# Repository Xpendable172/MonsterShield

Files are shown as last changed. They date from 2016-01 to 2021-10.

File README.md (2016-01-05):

# MonsterShield

    MonsterShield Prop Controller Editor software
    Copyright (C) 2015  Jason LeSueur Tatum

    This program is free software: you can redistribute it and/or modify
    it under the terms of the GNU General Public License as published by
    the Free Software Foundation, either version 3 of the License, or
    (at your option) any later version.

    This program is distributed in the hope that it will be useful,
    but WITHOUT ANY WARRANTY; without even the implied warranty of
    MERCHANTABILITY or FITNESS FOR A PARTICULAR PURPOSE.  See the
    GNU General Public License for more details.

    You should have received a copy of the GNU General Public License
    along with this program.  If not, see <http://www.gnu.org/licenses/>.

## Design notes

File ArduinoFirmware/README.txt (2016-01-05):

/**    
	MonsterShield Prop Controller Editor software
    Copyright (C) 2015  Jason LeSueur Tatum

    This program is free software: you can redistribute it and/or modify
    it under the terms of the GNU General Public License as published by
    the Free Software Foundation, either version 3 of the License, or
    (at your option) any later version.

    This program is distributed in the hope that it will be useful,
    but WITHOUT ANY WARRANTY; without even the implied warranty of
    MERCHANTABILITY or FITNESS FOR A PARTICULAR PURPOSE.  See the
    GNU General Public License for more details.

    You should have received a copy of the GNU General Public License
    along with this program.  If not, see <http://www.gnu.org/licenses/>.
**/

  MonsterShield Firmware Library V 1.5.0 {BETA}
  //////////////////////////////////////////////////////////////// 
  Released:   September 4, 2013
  Author:     Jason LeSueur Tatum
  
  HauntSoft 
  http://www.hauntsoft.com
  P.O. Box 1475
  Arlington Heights, IL 60006
  
  This library is intended to be used with the MonsterShield line of
  products produced by HauntSoft and is provided AS-IS.  This
  code has only been tested with Arduino UNO REV 3 microcontrollers,
  but may work with other Arduino compatible boards.
  
  The MonsterShield firmware is built around the "MonsterShield"
  class that provides access to all functionality and hardware.
  
  You are free to use this firmware in any way you see fit.  It 
  is as easy as instantiating a MonsterShield class object and 
  calling the "init()" function in your setup() routine.
  
  Tutorials and example solutions using this library
  will be made available over time on http://www.hauntsoft.com

  Arduino UNO R3 Pin Usage
  ===================================
  Digital I/O Pins
  ===================================
  13 LED2
  12 Keypad 0 (Prev      / Out 1)
  11 Keypad 1 (Next      / Out 2)
  10 Keypad 2 (Enable    / Out 3)
  9  Keypad 3 (Play/Stop / Out 4)
  8  Keypad 4 (Record)
  7  <---- Unused
  6  <---- Unused
  5  <---- Unused
  4  <---- Unused
  3  TX (Serial to MP3 module)
  2  RX (Serial from MP3 module, not connected)
  1  TX (Serial to host computer)
  0  RX (Serial to host computer)
  
  ===================================
  Analog I/O Pins
  ===================================
  A0 Trigger 0 (MonsterShield)
  A1 Trigger 1 (MonsterShield Expander)
  A2 Trigger 2 (MonsterShield Expander)
  A3 Trigger 3 (MonsterShield Expander)
  A4  SCL (i2c bus)
  A5  SDA (i2c bus)

  How to use the MonsterShield with the 1.5.0 firmware:
  =====================================================
  There are a few differences in how the MonsterShield 
  works with this new firmware compared to previous versions of the firmware.
  This is a quick guide to the new changes:
  
  Factory Reset:
  --------------
  1. Hold down the middle (prev/enable) button while pressing reset
  2. Release middle (prev/enable) button when "F" flashes rapidly
  3. When "F" flashes once per second, select number of desired slots
     by scrolling up and down with prev and nxt buttons.  Confirm
     desired number of slots by pressing mode/trigger button.
     Available options are: 1,2,3,4,5,6,7,8,9,A,B,C,D,E,F
     Note: If no selection is made for 10 seconds, then the value displayed
     will automatically be selected.
  4. Factory Reset will complete and the display will show "0" when done.
  
  Maximum slot length:
  ---------------------
  The maximum length of animation per slot depends on 2 factors:   
  1.  The number of slots the MonsterShield is configured for.
      You can perform a factory reset to change this number.  You can
      select 1 through 15 slots.
  2.  If you have the MonsterShield Expander board, you can increase
      the available slot length depending on whether you have 
      1, 2, or 3 total EEPROM chips installed.
  3.  A future version of the firmware will allow for larger EEPROM chips,
      but right now it is assumed that only the 24LC256 (32kbyte) chip
      is supported.
      
      Note:  The reason there is no difference between some slot
      numbers and/or chips is because we do not allow an animation
      to be split across multiple EEPROM chips.  We also enforce
      that all slots are equally sized.  There is also a requirement
      that each slot be divided evenly in 64-byte page increments.
      
This chart shows you your maximum available slot lengths:
slots	1 chip   2 chips  3 chips
15    00:54.4	 0:01:41  0:02:43
14    00:57.6	 0:01:55  0:02:43
13    01:02.4	 0:01:55  0:02:43
12    01:07.2	 0:02:16  0:03:23
11    01:13.6	 0:02:16  0:03:23
10    01:21.6	 0:02:43  0:03:23
9     01:29.6	 0:02:43  0:04:32
8     01:40.8	 0:03:23  0:04:32
7     01:55.2	 0:03:23  0:04:32
6     02:16.0	 0:04:32  0:06:48
5     02:43.2	 0:04:32  0:06:48
4     03:23.2	 0:06:48  0:06:48
3     04:32.0	 0:06:48  0:13:36
2     06:48.0	 0:13:36  0:13:36
1     13:36.0	 0:13:36  0:13:36
 
  Recording animation with the keypad:
  --------------------
  With previous versions of the firmware, all you had to do is press the 
  "record" button on the keypad and begin pressing the output buttons
  to record the animation.  With the new firmware, things are a bit
  more complex because there we've greatly increased the capabilities:
  
  * The new firmware supports the addition of up to 3 extra relay banks 
    (each bank contains 4 output relays) for a total of 16 relays when
    the MonsterShield Expander board is employed.
    
  * You can now record a single relay output at a time without affecting
    animation already recorded on the other tracks.  
    
  * You can now lay down additional recording on a track (overlay) 
    without losing the animation already stored on that track.  This can be
    used to extend an animation longer (up to the maximum length as given
    in the chart above)
    
  Recording steps:
  1.  Press the "record" button on the keypad.
  2.  "b" begins flashing.  This is bank-select mode.  Press 
      out 1, out 2, out 3, or out 4 to select banks 0, 1, 2, or 3.  Press
      "record" again to confirm.
  3.  "r" begins flashing.  This is relay-select mode.  Press
      out 1, out 2, out 3, or out 4 to select which relay on the selected
      bank you want to record.  If you'd like to record all 4 relays
      at the same time (like the old firmware), then skip this selection
      and just press "record" again.
  4.  "c" begins flashing.  This is the clear-option.  
      i.  Press out 1 to select overlay mode (record on top of track data)
      ii. Press out 2 to select clear track mode (erase selected track)
      iii.Press out 3 to select clear entire animation slot.

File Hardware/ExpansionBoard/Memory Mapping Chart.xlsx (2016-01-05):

memory | Control page size | avail mem | bytes per event | slots | Bytes per event | Pages | Actual bytes per slot | Actual events | Actual used memory | Wasted bytes | events/sec | Secs/Slot | Time/Slot | 2X Events | Bank 0 | Bank 1 |  |  |  |  | Bank 0 | Bank 1 | Bank 2
32768 | 128 | 32640 | 2 | 15 | 2176 | 34 | 2176 | 1088 | 32640 | 0 | 20 | 54.4 | 0:00:54 | 2176 | 7 | 8 | 4080 | 63 | 2016 | 0:01:41 | 5 | 5 | 5 | 6528 | 102 | 3264 | 0:02:43
32768 | 128 | 32640 | 2 | 14 | 2331 | 36 | 2304 | 1152 | 32256 | -384 | 20 | 57.6 | 0:00:58 | 2304 | 7 | 7 | 4662 | 72 | 2304 | 0:01:55 | 4 | 5 | 5 | 6528 | 102 | 3264 | 0:02:43
32768 | 128 | 32640 | 2 | 13 | 2510 | 39 | 2496 | 1248 | 32448 | -192 | 20 | 62.4 | 0:01:02 | 2496 | 6 | 7 | 4662 | 72 | 2304 | 0:01:55 | 4 | 4 | 5 | 6528 | 102 | 3264 | 0:02:43
32768 | 128 | 32640 | 2 | 12 | 2720 | 42 | 2688 | 1344 | 32256 | -384 | 20 | 67.2 | 0:01:07 | 2688 | 6 | 6 | 5440 | 85 | 2720 | 0:02:16 | 4 | 4 | 4 | 8160 | 127 | 4064 | 0:03:23
32768 | 128 | 32640 | 2 | 11 | 2967 | 46 | 2944 | 1472 | 32384 | -256 | 20 | 73.6 | 0:01:14 | 2944 | 5 | 6 | 5440 | 85 | 2720 | 0:02:16 | 3 | 4 | 4 | 8160 | 127 | 4064 | 0:03:23
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

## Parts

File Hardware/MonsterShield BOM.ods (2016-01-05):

 |  |  |  | # of Units: | 100 |  |  |  | 200 |  |  |  | 200 |  |  |  | 10
 |  |  |  |  |  |  |  |  | Imagineering |  |  |  | PCB Universe
MonsterShield PCB
MFG part# | Digikey part# | Reference # | Type | Unit quantity | Extend Qty | Unit Price | Extend Price | Cost per Unit | Extend Qty | Unit Price | Extend Price | Cost per Unit | Extend Qty | Unit Price | Extend Price | Cost per Unit | Extend Qty | Unit Price | Extend Price | Cost per Unit
 |  |  | PCB (MonsterShield) | 1 | 100 | 4.5 | 450 | 4.5 | 200 | 2.5 | 500 | 2.5 | 200 | 2.02 | 404 | 2.02 | 10 | 2.02 | 20.2 | 2.02
 |  |  |  |  |  |  | 450 | 4.5 |  |  | 500 | 2.5 |  |  | 404 | 2.02 |  |  | 20.2 | 2.02
MonsterShield Main Parts
MFG part# | Digikey part# | Reference # | Type | Unit quantity | Extend Qty | Unit Price | Extend Price | Cost per Unit | Extend Qty | Unit Price | Extend Price | Cost per Unit | Extend Qty | Unit Price | Extend Price | Cost per Unit | Extend Qty | Unit Price | Extend Price | Cost per Unit
A31412-ND | A31412-ND | RJ45 Keypad | RJ45 connector vertical | 1 | 100 | 0.7628 | 76.28 | 0.7628 | 200 | 0.69348 | 138.696 | 0.69348 | 200 | 0.62412 | 124.824 | 0.62412 | 10 | 0.884 | 8.84 | 0.01768
LA-401VN | 511-1531-ND (http://www.digikey.com/scripts/DKSearch/dksus.dll?Detail&itemSeq=116038993&uq=634756494036963984) | 7 Segment 10 DIP 7.62mm | 7 segment display, red | 1 | 100 | 1.575 | 157.5 | 1.575 | 200 | 1.4 | 280 | 1.4 | 200 | 1.225 | 245 | 1.225 | 10 | 1.96 | 19.6 | 0.0392
 | A100204-ND | 24LC256 | CONN IC socket vert 8POS Tin | 1 | 100 | 0.1255 | 12.55 | 0.1255 | 200 | 0.111 | 22.2 | 0.111 | 200 | 0.10618 | 21.236 | 0.10618 | 10 | 0.181 | 1.81 | 0.00362
 | 490-1532-1-ND | C1,C2,C3 | Ceramic Capacitor .1uF 0603 SMT | 3 | 300 | 0.0088 | 2.64 | 0.0264 | 600 | 0.00616 | 3.696 | 0.01848 | 600 | 0.0048 | 2.88 | 0.0144 | 30 | 0.00368 | 0.1104 | 0.0002208
 | A98037-ND | J1 Trigger | Screw terminal - 3 pins | 1 | 100 | 0.5595 | 55.95 | 0.5595 | 200 | 0.5108 | 102.16 | 0.5108 | 200 | 0.48648 | 97.296 | 0.48648 | 10 | 0.73 | 7.3 | 0.0146
 | 609-3263-ND | J2 Relays | Generic male header - 6 pins | 1 | 100 | 0.1563 | 15.63 | 0.1563 | 200 | 0.13824 | 27.648 | 0.13824 | 200 | 0.13222 | 26.444 | 0.13222 | 10 | 0.13222 | 1.3222 | 0.0026444
 | S5456-ND | J3 MP3 Module | Generic female header right angle- 20 pins | 1 | 100 | 0.9144 | 91.44 | 0.9144 | 200 | 0.84328 | 168.656 | 0.84328 | 200 | 0.762 | 152.4 | 0.762 | 10 | 1.219 | 12.19 | 0.02438
 | CP1-3524NG-ND | J4 Audio | Stereo Jack (TRS) 3.5mm | 1 | 100 | 0.3995 | 39.95 | 0.3995 | 200 | 0.323 | 64.6 | 0.323 | 200 | 0.323 | 64.6 | 0.323 | 10 | 0.595 | 5.95 | 0.0119
 | 475-1410-1-ND | LED1,LED2 | green smd LED | 2 | 200 | 0.059 | 11.8 | 0.118 | 400 | 0.05164 | 20.656 | 0.10328 | 400 | 0.0472 | 18.88 | 0.0944 | 20 | 0.074 | 1.48 | 0.00296
 | MCP23017-E/SS-ND | MCP23017 | SSOP28DB | 1 | 100 | 0.95 | 95 | 0.95 | 200 | 0.95 | 190 | 0.95 | 200 | 0.95 | 190 | 0.95 | 10 | 1.26 | 12.6 | 0.0252
 | P4.7KGCT-ND | R1, R2 | 4.7k Ω Resistor, 0603 SMT | 2 | 200 | 0.007 | 1.4 | 0.014 | 400 | 0.00384 | 1.536 | 0.00768 | 400 | 0.00256 | 1.024 | 0.00512 | 20 | 0.00152 | 0.0304 | 0.0000608
 | P1.0KGCT-ND | R3 | 1k Ω Resistor, 0603 SMT | 1 | 100 | 0.007 | 0.7 | 0.007 | 200 | 0.0052 | 1.04 | 0.0052 | 200 | 0.00384 | 0.768 | 0.00384 | 10 | 0.00152 | 0.0152 | 0.0000304
 | P220GCT-ND | R4, R5, R6, R7, R8, R9, R10, R11, R12, R13, R14, R15, R16, R17 | 150 Ω Resistor, 0603 SMT | 14 | 1400 | 0.00256 | 3.584 | 0.03584 | 2800 | 0.00256 | 7.168 | 0.03584 | 2800 | 0.00152 | 4.256 | 0.02128 | 140 | 0.00152 | 0.2128 | 0.0004256
 | SW402-ND | S1, S2, S3,RESET | Pushbutton | 4 | 400 | 0.23836 | 95.344 | 0.95344 | 800 | 0.18927 | 151.416 | 0.75708 | 800 | 0.18927 | 151.416 | 0.75708 | 40 | 0.2524 | 10.096 | 0.020192
 |  |  |  |  |  |  | 659.768 | 6.59768 |  |  | 1179.472 | 5.89736 |  |  | 1101.024 | 5.50512 |  |  | 81.557 | 8.1557
MonsterShield Additional parts
MFG part# | Digikey part# | Reference # | Type | Unit quantity | Extend Qty | Unit Price | Extend Price | Cost per Unit | Extend Qty | Unit Price | Extend Price | Cost per Unit | Extend Qty | Unit Price | Extend Price | Cost per Unit | Extend Qty | Unit Price | Extend Price | Cost per Unit
 | 24LC256-I/P-ND | 24LC256 | 24LC256 32k EEPROM chip | 1 | 100 | 0.81 | 81 | 0.81 | 200 | 0.81 | 162 | 0.81 | 200 | 0.81 | 162 | 0.81 | 10 | 0.88 | 8.8 | 0.88
 | SainSmart 4-Relay Module |  | SAINSMART | 1 | 100 | 8 | 800 | 8 | 200 | 8 | 1600 | 8 | 200 | 8 | 1600 | 8 | 10 | 8 | 80 | 8
 | 609-4453-1-ND | Female pins | Female pins for ribbon cable assembly | 12 | 1200 | 0.08494 | 101.928 | 1.01928 | 2400 | 0.08494 | 203.856 | 1.01928 | 2400 | 0.08494 | 203.856 | 1.01928 | 120 | 0 | 0 | 0
 | 609-2337-ND | 6-pin Connector housings | 6-pin Connector housings | 2 | 200 | 0.6232 | 124.64 | 1.2464 | 400 | 0.6232 | 249.28 | 1.2464 | 400 | 0.6232 | 249.28 | 1.2464 | 20 | 0 | 0 | 0
 | (futurelec GRCABLE10) | 6" ribbon cable | 6" ribbon cable (0.40 cents per 1 meter) | 1 | 100 | 0.07 | 7 | 0.07 | 200 | 0.07 | 14 | 0.07 | 200 | 0.07 | 14 | 0.07 | 10 | 0 | 0 | 0
 | 609-3249-ND | gold-plated headers, 6-pin | gold-plated headers, 6-pin | 2 | 200 | 0.2619 | 52.38 | 0.5238 | 400 | 0.2352 | 94.08 | 0.4704 | 400 | 0.2352 | 94.08 | 0.4704 | 20 | 0 | 0 | 0
 | 609-3300-ND | gold-plated headers, 8-pin | gold-plated headers, 8-pin | 2 | 200 | 0.2646 | 52.92 | 0.5292 | 400 | 0.2376 | 95.04 | 0.4752 | 400 | 0.2376 | 95.04 | 0.4752 | 20 | 0 | 0 | 0
 | 609-3465-ND | gold-plated breakaway 36-pin | gold-plated breakaway 36-pin | 1 | 100 | 0 | 0 | 0 | 200 | 0 | 0 | 0 | 200 | 0 | 0 | 0 | 10 | 0.707 | 7.07 | 0.707
 | Adafruit (206) | 6" cable with .100" 6 position | 6" cable with .100" 6 position | 1 | 100 | 0 | 0 | 0 | 200 | 0 | 0 | 0 | 200 | 0 | 0 | 0 | 10 | 1.5 | 15 | 1.5
 |  | Printed quickstart guide 1 page | Printed quickstart guide 1 page | 1 | 100 | 0.01 | 1 | 0.01 | 200 | 0.01 | 2 | 0.01 | 200 | 0.01 | 2 | 0.01 | 10 | 0 | 0 | 0
 |  |  |  |  |  |  | 1220.868 | 12.20868 |  |  | 2420.256 | 12.10128 |  |  | 2420.256 | 12.10128 |  |  | 110.87 | 11.087
Keypad PCB
MFG part# | Digikey part# | Reference # | Type | Unit quantity | Extend Qty | Unit Price | Extend Price | Cost per Unit | Extend Qty | Unit Price | Extend Price | Cost per Unit | Extend Qty | Unit Price | Extend Price | Cost per Unit | Extend Qty | Unit Price | Extend Price | Cost per Unit
 |  |  | PCB (Keypad) | 1 | 100 | 4.5 | 450 | 4.5 | 200 | 2.5 | 500 | 2.5 | 200 | 1.27 | 254 | 1.27 | 10 | 1.27 | 12.7 | 1.27
 |  |  |  |  |  |  | 450 | 4.5 |  |  | 500 | 2.5 |  |  | 254 | 1.27 |  |  | 12.7 | 1.27
Keypad Parts
MFG part# | Digikey part# | Reference # | Type | Unit quantity | Extend Qty | Unit Price | Extend Price | Cost per Unit | Extend Qty | Unit Price | Extend Price | Cost per Unit | Extend Qty | Unit Price | Extend Price | Cost per Unit | Extend Qty | Unit Price | Extend Price | Cost per Unit
 | A31442-ND | RJ45 Keypad | RJ45 connector right-angle | 1 | 100 | 1.0408 | 104.08 | 1.0408 | 200 | 0.94616 | 189.232 | 0.94616 | 200 | 0.85154 | 170.308 | 0.85154 | 10 | 1.206 | 12.06 | 1.206
 | SW402-ND | OUT1,OUT2,OUT3,OUT4,REC | Pushbutton | 5 | 500 | 0.2103 | 105.15 | 1.0515 | 1000 | 0.18927 | 189.27 | 0.94635 | 1000 | 0.18927 | 189.27 | 0.94635 | 50 | 0.2524 | 12.62 | 1.262
 |  |  |  |  |  |  | 209.23 | 2.0923 |  |  | 378.502 | 1.89251 |  |  | 359.578 | 1.79789 |  |  | 24.68 | 2.468
Packaging
MFG part# | Digikey part# | Reference # | Type | Unit quantity | Extend Qty | Unit Price | Extend Price | Cost per Unit | Extend Qty | Unit Price | Extend Price | Cost per Unit | Extend Qty | Unit Price | Extend Price | Cost per Unit | Extend Qty | Unit Price | Extend Price | Cost per Unit
 | SCP313-ND |  | Anti-static bag, 4" x 6" | 1 | 100 | 0.0612 | 6.12 | 0.0612 | 200 | 0.0612 | 12.24 | 0.0612 | 200 | 0.0612 | 12.24 | 0.0612 | 10 | 0.0612 | 0.612 | 0.0612
 |  |  | corrugated mailable white box (size?) | 1 | 100 | 1 | 100 | 1 | 200 | 1 | 200 | 1 | 200 | 1 | 200 | 1 | 10 | 1.5 | 15 | 1.5
 |  |  |  |  |  |  | 106.12 | 1.0612 |  |  | 212.24 | 1.0612 |  |  | 212.24 | 1.0612 |  |  | 15.612 | 1.5612
Optional Parts
Item # | Description |  | Source | Unit quantity | Extend Qty | Unit Price | Extend Price | Cost per Unit | Extend Qty | Unit Price | Extend Price | Cost per Unit | Extend Qty | Unit Price | Extend Price | Cost per Unit | Extend Qty | Unit Price | Extend Price | Cost per Unit
 | Arduino |  | AMAZON | 1 | 100 | 20 | 2000 | 20 | 200 | 20 | 4000 | 20 | 200 | 20 | 4000 | 20 |  |  |  |  | ARDUR3
A98374-ND | Term block Plug 3POS 3.5MM |  | DigiKey
A98397-ND | TermBlock Header 3Pos R/A 3.5MM |  | DigiKey
 | SainSmart 4-Relay Module |  | SAINSMART | 1 | 100 | 8 | 800 | 8 | 200 | 8 | 1600 | 8 | 200 | 8 | 1600 | 8
24LC512-I/P-ND | 512K EEPROM chip |  | DigiKey | 1 | 100 | 1.94
237-1449-ND | 9V .800A Power Supply Adapter |  | DigiKey | 1 | 100 | 5.56 | 556 | 5.56 | 200 | 5.56 | 1112 | 5.56 | 200 | 10 | 2000 | 10 |  | 5.56
993-1000-ND | 12V 2A Power Supply Adapter |  | DigiKey | 1 | 100 | 18.62 | 1862 | 18.62 | 200 | 18.86 | 3772 | 18.86 | 200 | 18.86 | 3772 | 18.86
237-1457-ND | 12V 2A Power Supply Adapter |  | DigiKey | 1 | 100 | 9.65 | 965 | 9.65 | 200 | 9.65 | 1930 | 9.65 | 200 | 9.65 | 1930 | 9.65
CP-2210-ND | 6' jack to plug 2.1mm x 5mm extension cable |  | DigiKey | 1 | 100 | 3.73 | 373 | 3.73 | 200 | 3.73 | 746 | 3.73 | 200 | 3.73 | 746 | 3.73 |  |  |  |  | CABYSP1
CP-2216-ND | 3' Jack to plug 2.1mm x 5mm extension cable |  | DigiKey
 | MP3 Module |  | MDFLY | 1 | 100 | 10 | 1000 | 10 | 200 | 10 | 2000 | 10 | 200 | 10 | 2000 | 10
 | 2GB SD Card |  |  | 1 | 100 | 10 | 1000 | 10 | 200 | 10 | 2000 | 10 | 200 | 10 | 2000 | 10 |  |  |  |  | SDCRD2GB
AE10490-ND | 7' Ethernet Cable |  | DigiKey | 1 | 100 | 3.367 | 336.7 | 3.367 | 200 | 3.367 | 673.4 | 3.367 | 200 | 10 | 2000 | 10 |  |  |  |  | CABETH1
Q364-ND | USB Cable 6' |  | DigiKey | 1 | 100 | 2.31 | 231 | 2.31 | 200 | 2.31 | 462 | 2.31 | 200 | 10 | 2000 | 10 |  |  |  |  | CABUSB1

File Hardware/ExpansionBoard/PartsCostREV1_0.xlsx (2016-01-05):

Digikey # | Description | Qty | Cost 1 | Cost 10 | Cost 25 | Cost 50 | Cost 100 | Cost 250 |  | Cost 50 Extended
S7039-ND | 6-pin female header | 2 | 0.69 | 5.37 | 12.51 | 22.75 | 40.95 |  |  | 40.95
S7041-ND | 8-pin female header | 1 | 0.87 | 6.76 | 15.74 | 28.63 | 51.53 |  |  | 28.63
S7043-ND | 10-pin female header | 1 | 0.83 | 6.86 | 15.88 | 28.58 | 50.8 |  |  | 28.58
A100204-ND | 8-pin DIP socket | 2 | 0.19 | 1.81 |  | 6.76 | 12.55 |  |  | 12.55
A106011CT-ND | 1K 1W carbon resisitor | 1 | 0.11 | 1.07 | 2 | 3.43 | 6.63 |  |  | 3.43
399-4151-ND | .1uF capacitor | 3 | 0.3 | 2.07 |  | 6.9 | 11.73 | 23.29 |  | 23.29
A98397-ND | TERM BLOCK HEADER 3POS R/A 3.5MM | 2 | 0.84 | 7.35 | 17.3 | 33.16 | 63.43 |  |  | 63.43
A98374-ND | TERM BLOCK PLUG 3POS 3.5MM | 2 | 1.89 | 17.11 | 40.16 | 76.82 | 146.66 |  |  | 146.66
MCP23017-E/SP-ND | MCP23017 | 1 | 1.44 | 12 | 25 |  | 91 |  |  | 50
609-3465-ND | .1" 36-pin break-away male headers | 1 | 0.8 | 7.07 | 16.63 | 31.87 | 60.96 |  |  | 31.87
24LC1025-I/P-ND | 128 KB EEPROM | 1 | 3.5 | 29.2 | 70.25 | ? | 270 |  |  | 270
PCB | PCB REV1.0 |  |  |  |  | 256 |  |  |  | 256
 | PCB rev0.0 (FAILED) |  |  |  |  |  | 277 |  |  | 277
 |  |  |  |  |  |  |  |  | Total | 1232.39
 |  |  |  |  |  |  |  |  | Per unit | 24.6478

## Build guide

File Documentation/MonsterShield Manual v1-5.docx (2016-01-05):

MonsterShield

User Manual

8/22/2013

Copyright © 2013 by HauntSoft

Written by Jason LeSueur Tatum

# Specifications & Features

- Modular components allow replacement of relay module, EEPROM, Arduino, and MP3 player
- Standard MonsterShield controls up to 4 devices with a single 4-relay module
- MonsterShield Expander board can be used to add 3 additional 4-relay modules for a total of 16 outputs.
- Each relay rated for both AC and DC current.
- Each relay supports up to 10 amps at 125VAC and 10 amps at 30VDC.
- All animations and settings are stored on user-replaceable non-volatile 32 kilobyte EEPROM chip(s). Standard MonsterShield supports a single EEPROM chip. MonsterShield Expander adds to additional EEPROM sockets.
- Supports up to 15 separate animations
- Each animation can be up to 13 ½ minutes long, depending on how many animation slots are configured and how many EEPROM chips are available (the MonsterShield Expander board adds 2 additional EEPROM sockets)
- Animation slots can be toggled as enabled or disabled with a push of a button on either the MonsterShield or with the detachable keypad.
- Animations can be manually triggered right from the MonsterShield or from the detachable keypad
- Detachable keypad connects using a standard network cable allowing you to stand in front of your prop while you program it
- Detachable keypad allows you to use 1 keypad with multiple MonsterShield-controlled props.
- Animations can be programmed by hand using the optional detachable keypad programmer, or they can be programmed visually using the powerful MonsterShield Editor software and a Windows computer.
- Optional MP3 module with SD card support for up to 8GB SD cards
- 4 different playback modes: sequential, single, random, and chain (chain not yet implemented)
- Ambient animation mode allows animation slot 0 to repeat continuously while waiting for a trigger
- Trigger supports voltages between 0.4 volts and 5 volts DC. Minimum trigger threshold can be configured in the MonsterShield Editor.
- Trigger can be configured to trigger on LOW voltage or HIGH voltage.
- Trigger can be configured to ignore repeated triggers if the input voltage has not returned to its un-triggered state. This prevents endless triggering if a beam sensor is knocked out of alignment with its reflector.
- Trigger supports a “cool down” feature that prevents frequent triggers. This can be set between 0 to 255 seconds.
- Trigger supports an adjustable sensitivity setting to help eliminate false triggers. This can be configured in increments of 10 milliseconds up to 2550 milliseconds.
- MonsterShield has a built-in serial interface that allows developers to write their own software to control the MonsterShield while connected to a computer via the USB port. You can use the MonsterShield for other applications, such as home automation!
- MonsterShield Editor allows you to download all animations to and from the MonsterShield. You can save the animations to a file for backup.
- MonsterShield hardware can be hacked to add additional features. There are several unused pins from the Arduino that you could utilize for your own purposes. The RJ-45 connector also has an unused digital I/O pin and there are +5 and GND pins on the connector as well. For ultimate ease in hacking, the MonsterShield Expander board (optional purchase) has female headers for all Arduino pins for easy access.
- The MonsterShield firmware (Arduino code) is now built around the all-new MonsterShield library that can be used by advanced users to fit almost any custom need.

# Using the MonsterShield

## Getting Started

The base MonsterShield prop controller consists of 3 major components:

- MonsterShield board
- Arduino
- Relay module

In addition to these 3 major components, there are optional components are available:

- MP3 module
- Detachable programming keypad
- MonsterShield Expander board

Items not shown:

- External power supply
- Ethernet cable (not included, used with the detachable keypad)
- USB cable (optional)

## Quick Start Guide

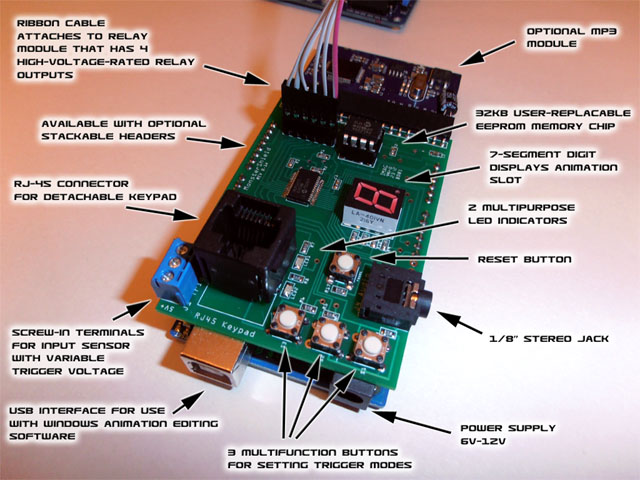
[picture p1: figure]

1. Connect MonsterShield to Arduino: Carefully connect the Arduino to the MonsterShield. The MonsterShield has 2 banks of 8 pins and 2 banks of 6 pins on the bottom of the board that are designed to connect to the Arduino. Hold the Arduino in one hand and hold the MonsterShield in the other. Line up the MonsterShield so that the end with MP3 module connector is opposite the end on the Arduino that has the power & USB connectors. Make sure that the right-most pins on the MonsterShield line up with the right-most headers on the Arduino. Make sure the pins are lined up and seat the MonsterShield all the way down. Note that some Arduinos can accept additional pins that the MonsterShield does not have, but this is not an issue. It should look like this when properly connected:
2. Connect Relay Module to MonsterShield: Connect one end of the included 6-wire cable to the J2 6-pin header and insert the other end of the cable on the header on the relay module so that the same colored wire matches the GND label on both the MonsterShield and the relay module. For consistency, it is recommended that the black wire be on the end that matches GND on both sides.
3. Connecting devices to be controlled by the relays: How you connect devices to the relays depends on what devices you plan to control and what the power requirements are. You can connect devices to be normally closed (power is on normally, but power switches off when relay is turned on) or normally open (power is off normally, but power switches on when relay is turned on). Here are some common ways to connect devices to the relay module:

MonsterShield and Four 12V solenoid valves powered with 12V 2A power supply

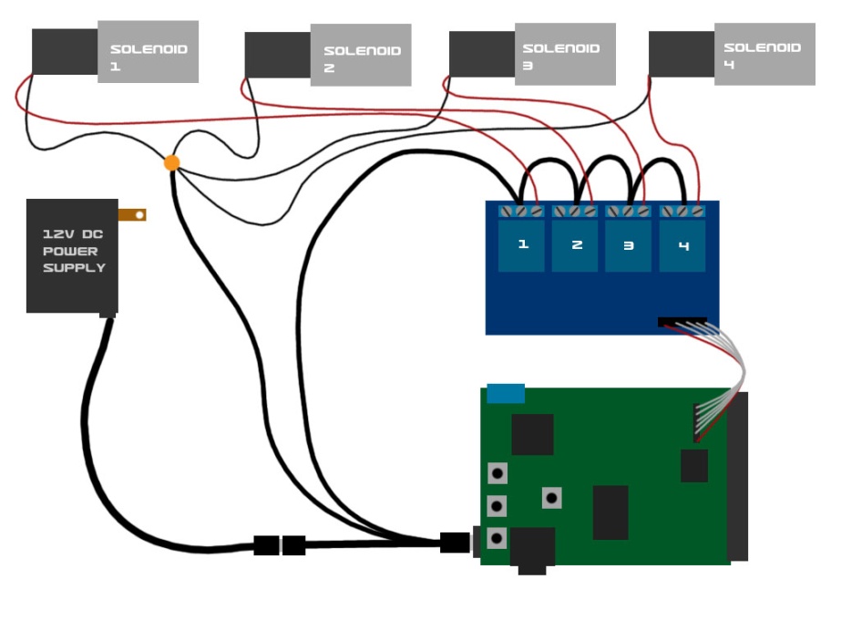
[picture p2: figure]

MonsterShield and solenoid valves powered separately

2 solenoid valves powered separate and 1 AC output

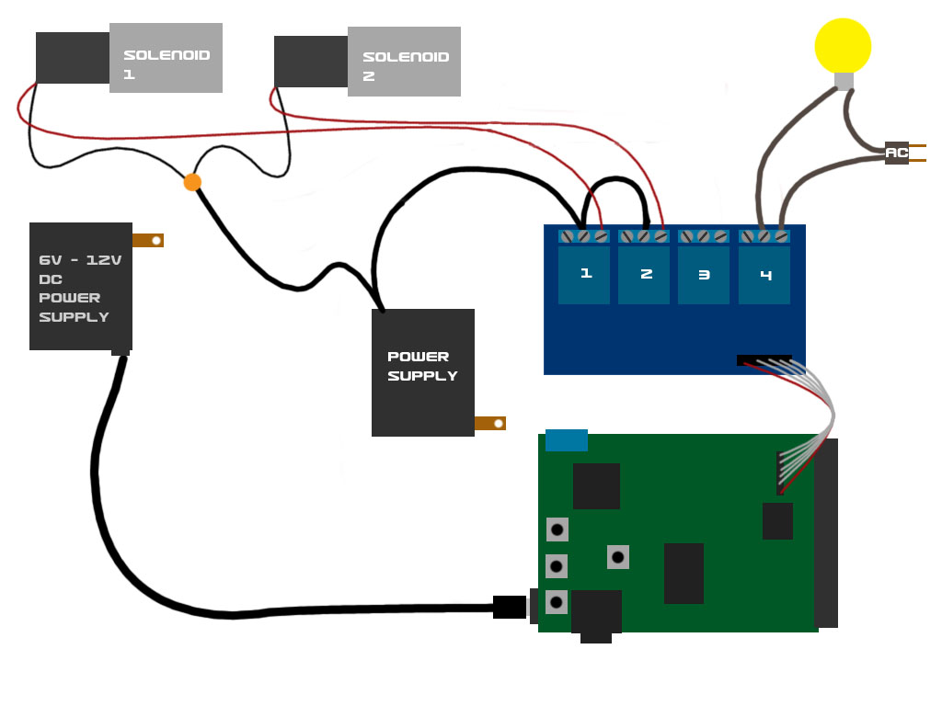
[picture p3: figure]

4. Connect Trigger: Connect a trigger (such as a motion sensor, push button, or beam sensor) to the J1 blue screw terminals on the MonsterShield. The screw terminals are labeled as +5V, Trigger, and GND. Note that some trigger types only require the +5 and the Trigger terminals (such as a beam sensor or a push button). Triggers that require +5V to operate will use all 3 terminals (such as the Parallax PIR motion sensor). If your trigger has different power requirements (such as a beam sensor that requires 12V), you will need to connect a separate power supply to the trigger (or if it is a 12V trigger you can use the 12V 2A power supply and the splitter cable to provide power to the trigger) and you use the +5V and the Trigger terminals on the switched leads for the trigger. For example, the Fright Props beam sensor has 5 wires. Two wires supply 12V power to the sensor. The other 3 wires are common, normally open, and normally closed. You would use only the common and normally open or the common and normally closed (but not all 3 at the same time), and these would be wired to the +5V and the Trigger terminals, but it doesn’t matter which wire goes to which of the terminals.

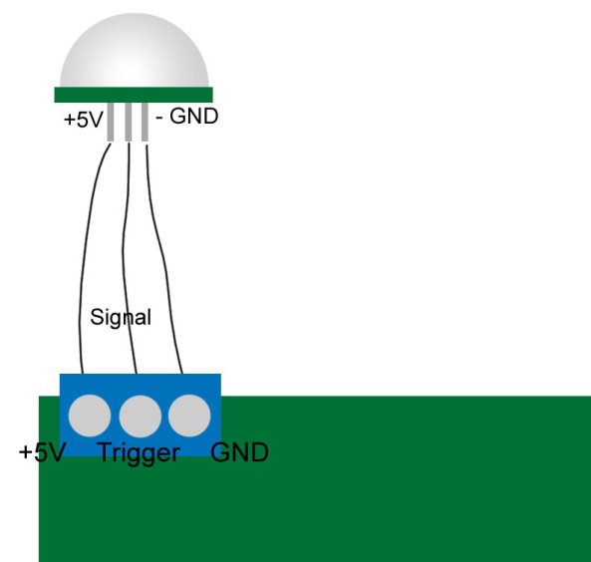
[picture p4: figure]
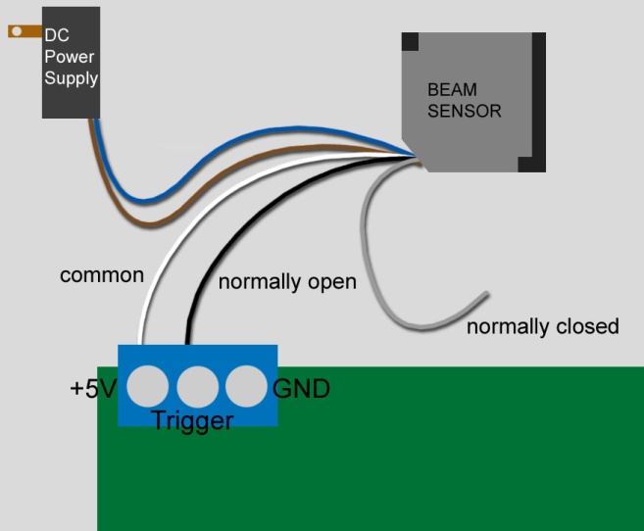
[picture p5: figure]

5. Connect Optional MP3 module: If you purchased the optional MP3 module, connect it to the J3 MP3 Module header on the MonsterShield so that the SD card slot is on the bottom. Note that it is easier to install and remove the SD card from the MP3 module with the MP3 module removed from the MonsterShield. Copy MP3 files to your SD card and name them 000.mp3 through 014.mp3. The 3 digit number corresponds to the animation slot it will be played with.

Connect a 1/8” stereo jack to the MonsterShield and connect this to a powered amplifier or speaker system. Note that the output from this jack is headphone level, which means it is pre-amplified for headphones. This may cause damage or distortion to sensitive equipment that is not designed to handle this level. This can be addressed by using a small adapter cable that has a built-in volume control. Adjust the volume until the distortion disappears.

6. Connect Power to Arduino: Connect your power source (6V DC to 12V DC) to the Arduino. If you are using the 12V 2A power supply and the optional splitter cable, connect the splitter cable between the power supply and the Arduino. Make sure that the bare leads on the other end of the cable are not touching each other. The MonsterShield will power up and should display “-“ for a second or two. When complete, the MonsterShield should display a “0” or some other slot number that was previously selected when the MonsterShield was previously powered up. If the single digit display does NOT display any digit and LED2 is flashing on and off, then this means you have not loaded the MonsterShield code onto the Arduino. You will need to download the firmware from http://www.hauntsoft.com/downloads and you will need to install it using the Arduino IDE (which can be obtained from http://www.arduino.cc).
7. Using the optional keypad: Attach the optional keypad using a standard cat5 network cable. When connected, the keypad has two modes: Normal & Record.
  a. In Normal mode, you can cycle through all the animation slots by using the first 2 buttons (next and previous). The 3rd button acts as a toggle for enabling or disabling the currently selected animation slot. The 4th button manually triggers the prop. Pressing the 4th button while an animation is running will stop the animation.
  b. Pressing the 5th button will prepare the MonsterShield to record animation on the currently selected slot. See the Recording Animation below.

Now test your animation by pressing the play button.

8. Manually triggering your prop: Press the “mode/trigger” button on the MonsterShield or the “play/stop” button on the keypad to manually trigger your prop. Pressing these buttons again will interrupt and stop the animation from playing.
9. Selecting an animation slot: Press and release the “prev/enable” button or the “next/ambient” buttons on the MonsterShield repeatedly to cycle through the animation slots. Don’t hold these buttons down because this activates their secondary functions. You can also press the “Prev” and “Next” buttons on the keypad to cycle through the animations.
10. Recording an animation: Select the animation slot you wish to record and press the Record button on the keypad. You will first be prompted to make 3 selections:
  a. Bank Selection: First the MonsterShield will begin flashing the letter “b” on the display. This is the bank selection prompt. Press the Out 1 button to select bank 0 on the MonsterShield. If you have a MonsterShield Expander board connected, you could also press Out 2, Out 3, or Out 4 to select banks 1, 2, or 3. The selected bank number will begin flashing. Press and release the record button to confirm the selected bank. Note: If you do not have a MonsterShield Expander board attached, you could skip this and just press the record button and bank 0 will be selected automatically.
  b. Relay Selection: Now the MonsterShield will begin flashing the letter “r” on the display. This is the relay selection prompt that allows you to select which relay output / track you want to record animation to. If you would like to record animation on all relays for the selected bank, just press the record button again. If you would like to only record animation for a single relay on the bank (and ignore inputs on the other relays), then select the relay you want to program by pressing Out 1, Out 2, Out 3, or Out 4. Press the record button to confirm the relay selection.
  c. Record Mode: Now the MonsterShield will begin flashing the letter “c” on the display. This is the recording mode prompt. There are 3 options:
    i. Mode 0: Overlay – This lays down animation on top of what was already previously recorded. If you had previously recorded events on the selected relay/tracks but want to record addition events on the same track, you can use this option. During recording, previous events on these relays/tracks will be played while allowing you record new events on top.
    ii. Mode 1: Wipe selected relay track – This clears all previous animation from the selected relays/tracks but keeps the animation data for all the other relays/tracks.
    iii. Mode 2: Wipe entire animation – This clears all of the animation for all banks and all relays letting you start from scratch for this animation.

Press Out 1, Out 2, or Out 3 to select the recording mode you desire. Then press the Record button to begin recording the animation.

The letter “P” will begin flashing on the display to indicate you are now in Record Program mode. Press and release the Out 1, Out 2, Out 3, and Out 4 buttons to turn the relay outputs on and off as desired. When finished recording, press the Record button again.

11. Disabling or Enabling an animation slot: Select the animation slot you want to enable or disable. You can tell if an animation slot is enabled or disabled by the decimal point on the single digit display. If a slot is enabled, the decimal point will be lit. To toggle the slot between enabled & disabled, simply press and hold the “prev/enable” button on the MonsterShield for 1 second and then release. You can also press the “enable” button on the keypad to toggle the slot.
12. Setting Playback mode: There are currently 3 playback modes: Sequential, Single, & Random. You can cycle between the playback modes by pressing and holding the “mode/trigger” button on the MonsterShield for more than 1 second and releasing. The MonsterShield will flash “P” and “1”, “2”, or “3”. “1” means sequential mode (the default). Each time the prop is triggered, the MonsterShield will advance to the next slot after the animation has finished playing. “2” means random mode. Each time the prop is triggered, the MonsterShield will randomly select which animation to play. “3” means single mode. The MonsterShield will stay on this slot every time it is triggered. If Ambient mode is turned on, then slot 0 will never be selected when the prop is triggered.
13. Ambient mode: Ambient Mode turns animation slot 0 into an ambient animation that plays in a continuous loop. When the prop is triggered, the slot 0 animation is interrupted and the triggered animation plays. When the triggered animation is finished, the MonsterShield will go back to playing animation slot 0 in a continuous loop. You can toggle the ambient animation on & off by pressing and holding the “nxt/ambient” button on the MonsterShield for more than 1 second and releasing. WARNING: Make SURE you have recorded an animation on slot 0 before turning ambient mode on. If you forget to do this, the MonsterShield could go into an endless loop that cannot be interrupted. You will have to perform a factory reset which will initialize all settings to the defaults and will wipe out all animation on the MonsterShield. If the letter “E” flashes for several seconds when you attempt to turn on Ambient mode, it means the MonsterShield detected no animation on slot 0 and aborted the Ambient mode.
14. Performing a Factory Reset: If you need to perform a factory reset, press and hold the “prev/enable” button on the MonsterShield and then press and release the “reset” button while continuing to hold the “prev/enable” button. The MonsterShield will reset and begin performing a factory reset to the defaults. When the letter “F” begins rapidly flashing, you may release the “prev/enable” button. After a few seconds, the MonsterShield will begin flashing “F” once a second. This is prompting you to confirm how many animation slots you want to configure on the MonsterShield. Your options are 1, 2, 3, 4, 5, 6, 7, 8, 9, A (10), B (11), C (12), D (13), E (14), and F (15). F is the default. You can cycle through the available selections using the “prev/enable” and “nxt/ambient” buttons. To confirm your selection, press the “mode/trigger” button. If no user selection is made after 10 seconds, then the MonsterShield will configure itself to the default of 15 slots. Generally speaking, the fewer slots you configure the MonsterShield for, the longer each animation can be.
15. Connecting to your computer: Before you can begin using the MonsterShield with your computer, you will have to install the Arduino drivers. These drivers are included and automatically installed with the MonsterShield software version 1.0.0.4 and later. The drivers are also available by downloading the Arduino IDE:
  a. Download the Arduino IDE from http://www.arduino.cc and unzip it to your computer.
  b. Connect the MonsterShield to your computer using a standard USB printer cable. Windows will detect that a new piece of hardware has been added. You will need to tell Windows to look in the Arduino directory’s “drivers” subdirectory.
  c. Windows should then find and install the appropriate driver for your Arduino.

## Connecting Modules & Cables

### Attaching MonsterShield to an Arduino

The first step is to connect the MonsterShield board to an appropriate Arduino (such as the Arduino UNO R3). Please note that the MonsterShield will not function without an Arduino.

The MonsterShield has 2 banks of 6 male pins and 2 banks of 8 male pins on the bottom of the board for plugging into an Arduino. Some Arduinos (such as the Arduino UNO R3) have 2 additional pin positions on both of the leftmost female headers that are not used by the MonsterShield. When connecting the MonsterShield to an Arduino, make sure that the rightmost pins on the MonsterShield match up with the rightmost female pin sockets on the Arduino. Push the MonsterShield all the way down so that it is seated snug on top of the Arduino. This is what the MonsterShield should look like after attaching to the Arduino:

### Connecting the Relay module to the MonsterShield

Connect the Relay Module to the MonsterShield using the supplied 6-pin ribbon cable.

STEP 1: Connect one end of the cable to the 6-pin male connector labeled “J2 Relays” on the MonsterShield, ensuring that the red wire is towards the left of the “J2 Relays” label.

STEP 2: Connect the other end of the cable to the 6-pin male connector on the relay module ensuring that the red wire is on the pin labeled “GND”.

WARNING: IMPROPERLY CONNECTING THIS CABLE CAN DAMAGE YOUR MONSTERSHIELD AND/OR ARDUINO!

### Connecting the MP3 module (optional) to the MonsterShield

If you purchased the MP3 module, you can connect that to the MonsterShield now. Do not connect or disconnect the MP3 module while the MonsterShield is powered on.

Insert the MP3 module into the 20-pin female connector on the right edge of the MonsterShield. The SD card should be on the bottom of the MP3 player when connecting the MP3 module. Note that it is easier to install and remove the SD card from the MP3 player when the MP3 player is removed from the MonsterShield.

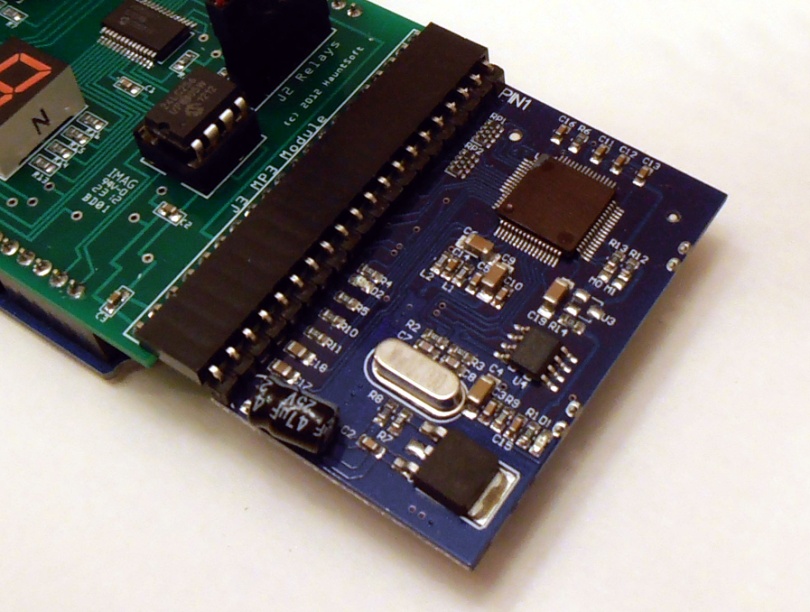
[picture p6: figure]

The MP3 module will not do anything without an SD card loaded with MP3 files. Before using the MP3 module, you should load MP3 files onto a standard 1GB, 2GB, 4GB, or 8GB SD card. In order for the MP3 player to work properly, you need to rename your MP3 files in the following way:

000.mp3 | Slot 0
001.mp3 | Slot 1
002.mp3 | Slot 2
003.mp3 | Slot 3
004.mp3 | Slot 4
005.mp3 | Slot 5
006.mp3 | Slot 6
007.mp3 | Slot 7
008.mp3 | Slot 8
009.mp3 | Slot 9
010.mp3 | Slot A (10)
011.mp3 | Slot B (11)
012.mp3 | Slot C (12)
013.mp3 | Slot D (13)
014.mp3 | Slot E (14)

As an example, whenever animation slot 5 is activated, the corresponding 005.mp3 file will be played. You do not have to have every file. Missing files simply means there won’t be any sound for those particular animation slots.

Note that you can also use the MonsterShield Editor on a Windows OS computer to simplify this task. The MonsterShield Editor has a “MP3” tab. On this tab, there is a button to select your MP3 files and another button to copy all of the chosen files to your SD card reader. The software will take care of renaming the files on the SD card for you.

Note: It has come to our attention that the MP3 module is finicky about how the files are loaded on the SD card. We have discovered that the MP3 module ignores the filenames and instead numbers the files internally based on the order they are copied to the SD card. So you copy 3 MP3 files to the SD card, and then later copy the first MP3 file to the same card replacing the file that was there before, the MP3 player will think the newly copied file is file #3. This will result in the wrong sound files being played with your animations. The easiest way to solve this problem is to always re-copy all MP3 files to the SD card at the same time. Our editor also does this for you if you use the Copy MP3 files option.

### Connecting Audio

The MonsterShield has a 3.5mm stereo jack for audio out. Connect your amplifier or amplified speakers to this jack. Note that the output from this jack is slightly amplified for headphone use. Because of this, some amplifiers may be distorted from too strong a signal. If you experience this, the distortion can be eliminated by using a cable with a volume control on it. Adjust the volume knob on the cable until the distortion is removed.

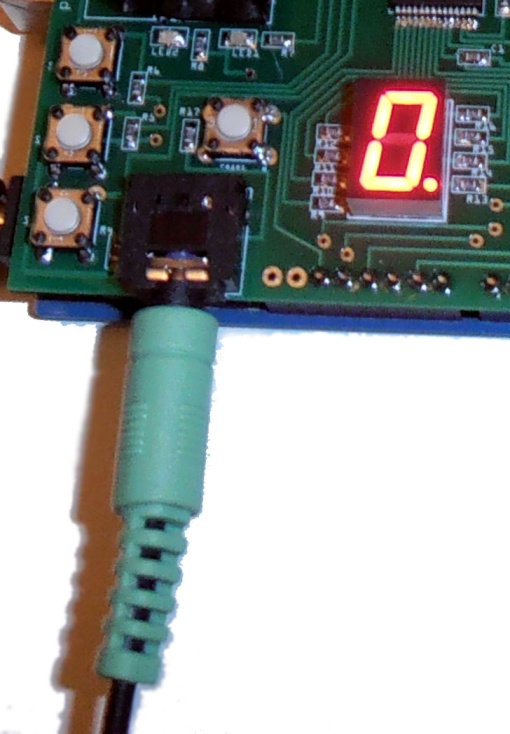
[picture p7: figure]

### Connecting a Trigger

There are 3 screw terminals housed in a blue connector labeled “J1 Trigger”. This is for connecting a trigger to the MonsterShield, such as a push button, motion sensor, pressure mat, etc. The 3 terminals are labeled as:

+5V

TRIGGER

GND

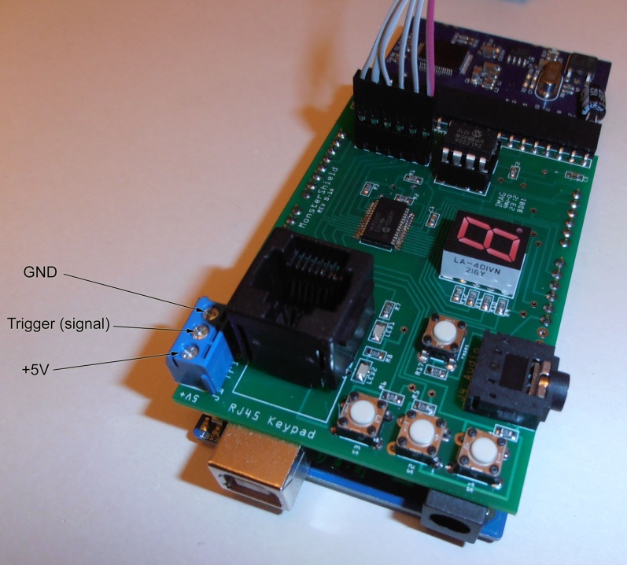
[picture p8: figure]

By default, in order to trigger the prop, the TRIGGER terminal will need to see between 3V and 5V. You can adjust the minimum voltage threshold using the MonsterShield Editor. You can test the trigger by simply using a jumper wire and touching the +5V terminal and the TRIGGER terminal at the same time.

#### How to connect a push button trigger:

A push button trigger normally requires 2 wires. Connect 1 wire to the +5V and the other wire to the TRIGGER. Pressing the button “closes” the circuit and causes the prop to be triggered.

#### How to connect a motion sensor:

Check your motion sensor and see what its power requirements are and make sure the signal wire for the motion sensor does not output more than 5V. WARNING: The Arduino and/or MonsterShield may be damaged if you send more than 5V to the TRIGGER terminal! A motion sensor that works well is the Parallax motion sensor. This motion sensor has 3 pins labeled +, signal, -. Connect the motion sensor the MonsterShield trigger via a cable. Connect the + to the +5V screw terminal on the MonsterShield trigger and the – to the GND screw terminal on the MonsterShield trigger, and connect the signal to the TRIGGER screw terminal on the MonsterShield.

#### How to connect a beam sensor:

A beam sensor usually requires separate power and can’t be powered from the +5V connection on the MonsterShield. If your beam sensor works with 12V, you can use the 12V 2A power supply and splitter cable sold by HauntSoft to power your beam sensor. Beam sensors usually work like a light switches and merely complete the circuit on 2 wires when the beam is broken. Most beam sensors will have 5 wires, and you’ll likely only need to use 4 of them. 2 wires are for powering the beam sensor, and 2 wires are for connecting the output. One of the output wires will be the “common” wire and the other output wire you will use will be either the “normally open” wire or the “normally closed” wire. Which wire you use depends on how you want to use the beam sensor and how you configure the trigger on the MonsterShield. If you use the “normally open” wire, electricity will flow between the common wire and the normally open wire only when the beam is broken. You should set the trigger mode to “HIGH” in the MonsterShield Editor (this is also the factory default). If you want to use “normally closed”, then electricity flows between the common and the normally closed wire until the beam is broken, at which point electricity stops flowing. You will need to set the trigger mode to “LOW” in the MonsterShield Editor.

#### How to connect a pressure mat sensor:

A pressure mat normally requires 2 wires. Connect 1 wire to the +5V and the other wire to the TRIGGER. Applying pressure to the mat “closes” the circuit and causes the prop to be triggered.

### Connecting Power

Connect an external power supply with a barrel-style connector to the Arduino. The power supply should be rated for 6V – 12V DC and at least 650 mA. We recommend the 12V 2A power supply if you intend to power 12V solenoid valves and/or 12V sensors from the same power supply that is providing power to the MonsterShield.

Note: When connecting the MonsterShield to your computer, you can disconnect the external power supply from the Arduino although this is not necessary. The Arduino will get its power from the USB cable. Also note that you may hear some static on the audio from the MP3 module on the MonsterShield when the relays are being switched on and off while the MonsterShield is being powered by the USB cable. This is because the USB cable does not provide enough power to operate the MP3 player without distortion. This distortion should go away when powered externally with a sufficient power supply.

### Connecting devices to the relays

The relay module is where you will connect the devices that will be controlled by the MonsterShield. The relays on the relay module are rated for up to 30VDC at 10 amps and 125VAC at 10 amps. This will allow you to control just about anything. Examples include:

- Solenoid valves for pneumatics (12V or 24V are the most common)
- AC or DC lights
- AC or DC motors
- Fog machine triggers
- Flood lights

WARNING: Please use CAUTION when controlling AC current with the MonsterShield. There is risk of shock or electrocution when controlling AC current with the relays. Never come into contact with any part of the relay module when powered by AC current.

WARNING: Please be aware that the current controlled by the relays is external to the MonsterShield and there could be live current going to the relays even with the MonsterShield unplugged. Because of this, assume that there is always a shock hazard or risk of electrocution even when the MonsterShield is unpowered!

Devices can be connected to the Relays on the Relay modules in two ways. You can connect a device so that it is normally closed (current flows until when the relay is turned off and current stops when the relay is turned on) or you can connect a device so that it is normally open (current only flows when the relay is turned on).

For most devices, you will connect only 2 wires to a relay.

In the following diagram, there are 4x 12V solenoids that are being powered by the same 12V 2A power supply that is powering the MonsterShield. Note that a splitter cable is being used that has a branch that is powering the solenoids:

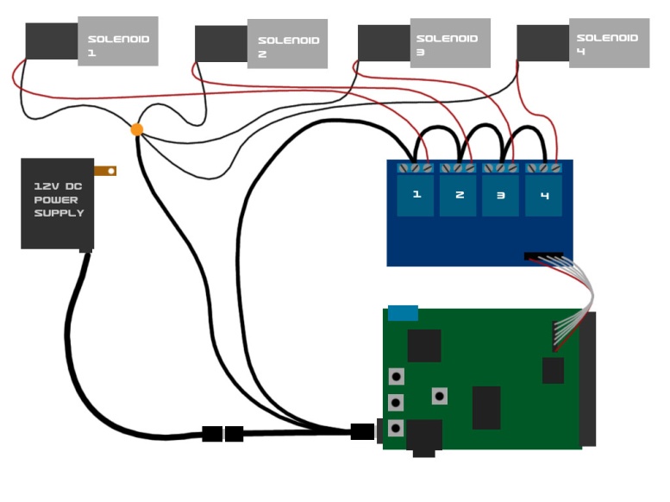
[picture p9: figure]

In this diagram, the solenoids are being powered by a separate power supply from the power supply that is powering the MonsterShield:

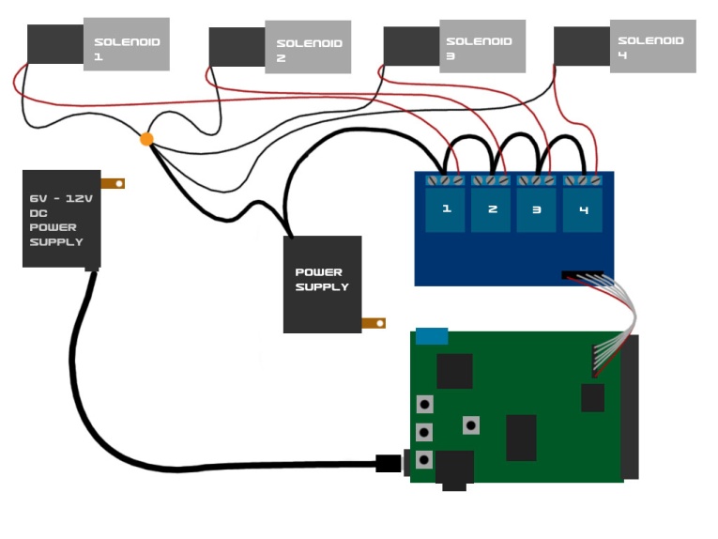
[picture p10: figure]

Finally, in this diagram, 2 solenoids are being powered by a separate power supply and 1 AC light is being powered by an AC plug. Please use extreme caution when connecting AC lines to the relay module!

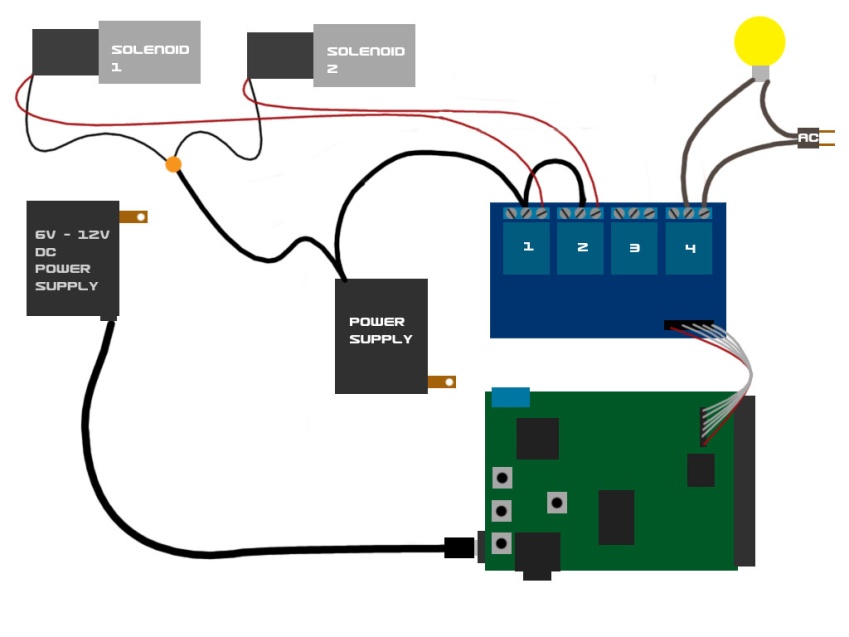
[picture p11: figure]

## Operating the MonsterShield

### Using the on-board buttons

There are 3 multi-purpose buttons on the MonsterShield plus a reset button. The following is a brief description of each button and its uses:

#### MODE / TRIGGER

Pressing this button will manually trigger the MonsterShield to begin playing an animation.

Pressing and holding this button for at least 1 second and releasing (long-pressing) will cycle through the next playback mode. The MonsterShield has the following playback modes:

1 | Sequential – Each time prop is triggered, MonsterShield advances to the next enabled slot after the animation has finished playing.
2 | Single – Each time prop is triggered, the currently selected animation slot plays.
3 | Random – Each time prop is triggered, the MonsterShield will randomly select the next animation slot to play the next time it is triggered.

Each time this button is long-pressed, the MonsterShield will advance to the next playback mode and will flash the number shown in the left column of the table above for the currently selected playback mode for several seconds.

#### PREV / ENABLE

Pressing this button will select the previous animation slot. If the MonsterShield was currently on animation slot 5, pressing this button will make slot 4 the current slot, and the number “4” will be shown on the single digit display.

Long-pressing this button will toggle whether the currently selected animation slot is enabled or disabled. A disabled animation slot will never be played by the MonsterShield. You can tell if an animation slot is enabled or disabled by the decimal point on the bottom right corner of the single digit display. If the decimal point is lit, then the currently selected animation slot is enabled. If the decimal point is not lit, then the currently selected animation slot is disabled.

#### NXT / AMBIENT

Pressing this button will advance to the next animation slot. If the MonsterShield was currently on animation slot 5, then pressing this button will advance to animation slot 6 and the number “6” will be shown on the single digit display.

Long-pressing this button will toggle Ambient mode on & off. When Ambient mode is on, the MonsterShield will play animation slot 0 in a continuous loop without being triggered. Once the prop is triggered, then the MonsterShield will stop playing animation slot 0 and will begin playing one of the other animation slots (1 through E) as appropriate for the currently selected playback mode. Once that animation has finished playing, the MonsterShield will go back to playing animation slot 0 in a continuous loop. When ambient mode is turned on, the left green LED on the MonsterShield will flash continuously twice per second. Long-pressing this button again will turn off ambient mode and animation slot 0 will stop playing.

#### RESET

Should the MonsterShield ever lock-up or behave erratically, pressing this button will reset the Arduino / MonsterShield. Sometimes when connecting an external power supply, the Arduino needs to be reset once. You can tell if you need to do this if the single digit display does not light up after a couple of seconds.

#### PERFORMING A FACTORY RESET

If you need to perform a factory reset, press and hold the “prev/enable” button on the MonsterShield and then press and release the “reset” button while continuing to hold the “prev/enable” button. The MonsterShield will reset and begin performing a factory reset to the defaults. When the letter “F” begins rapidly flashing, you may release the “prev/enable” button. When the flashing stops the MonsterShield should be on slot 0. The Factory Reset is now complete.

### Using the optional keypad

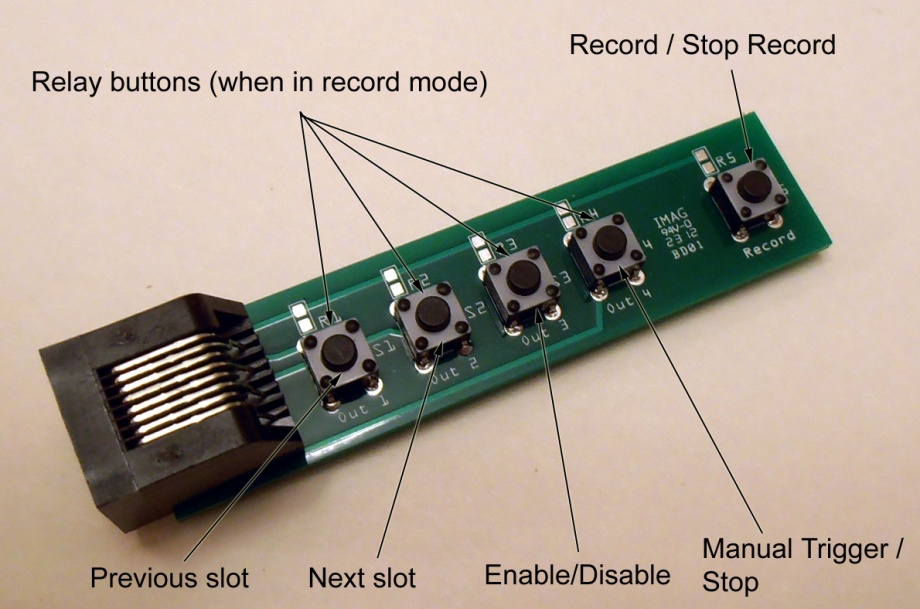
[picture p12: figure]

To use the optional keypad, simply attach a standard Cat5 or Cat6 network cable between the keypad and the MonsterShield. The keypad and the MonsterShield both have RJ-45 connectors for this purpose. You can use any length of network cable up to 25 feet. We have not tested network cables longer than 25 feet, but they might still work. Note that you do not need to power off the MonsterShield when attaching or detaching the keypad. It is designed for this purpose so that you can quickly detach it from MonsterShield and connect it to another MonsterShield without having to shut off the power.

The keypad has two modes: Normal mode & Record mode.

#### Normal Mode

When the MonsterShield is not in record mode, it is in Normal Mode. When in Normal Mode, the keypad has several useful functions. You can cycle through all of the animation slots using the Previous slot and next slot buttons. You can toggle whether an animation slot is enabled or disabled by pressing the enable/disable button. You can manually trigger a prop animation to play by pressing the Manual Trigger button. You can also force an animation to stop playing by holding down the Manual trigger button for more than 1 second and releasing.

#### Record Mode

You enter Record Mode by pressing the Record button. The currently selected animation slot shown on the single digit display will begin flashing and the associated MP3 file will start playing (if MP3 module is present and associated file exists on the SD card). You can start activating the relays by pressing the 4 input buttons. Holding a button down will keep the relay on until the button is released. The MonsterShield will accurately record every input you do along with the actual timings. When you are finished recording the animation simply press the Record button a second time. This animation is now stored on the MonsterShield’s EEPROM memory chip and will be saved even if you remove power from the MonsterShield.

# MonsterShield Editor Software

The MonsterShield Editor software is available for download from the http://www.hauntsoft.com

This software allows you to access the advance features of the MonsterShield and allows you to visually see and edit all of the animations on the MonsterShield. You can download previously recorded animations from the MonsterShield, or upload new animations that you’ve created using the editor. You can also backup all your animations to a file for safe keeping.

## Installing the software

Download the MonsterShield Editor from http://www.hauntsoft.com and install on a Windows XP, Windows Vista, or Windows 7 computer. Run the setup program and follow the on-screen prompts.

The first time you launch the MonsterShield Editor, you may be asked to enter your registration code. This should have been emailed to you when you placed your order.

## Launching the MonsterShield Editor

Double-click the MonsterShield Editor icon after installing the software. When you first launch the editor, this is what you will see:

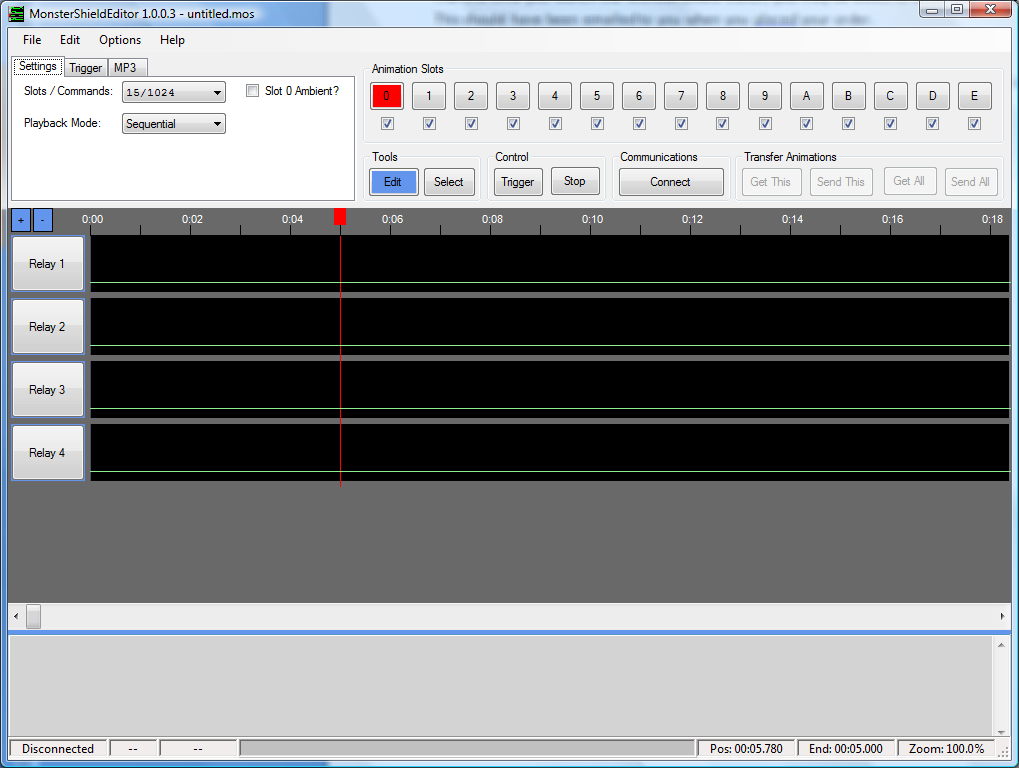
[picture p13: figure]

While it is not necessary to have the MonsterShield connected to your computer when you launch the editor, it is recommended. Adjusting settings on-screen will adjust them on the MonsterShield in real-time if the MonsterShield is connected.

Select the COM port for your MonsterShield by going to the Options -> Com Port menu and selecting the appropriate com port for you MonsterShield:

Click the Connect button to connect to your MonsterShield. You should see the message “Successfully connected to the MonsterShield” in the status bar. If the software failed to connect to your MonsterShield, you will see a red error message in the status bar. Example:

After you have successfully connected to the MonsterShield, you can test the relays simply by clicking on the 4 Relay buttons on the left side of the screen. You should see the appropriate indicator light flash on the relay module. Press and hold the left mouse button will keep the relay on for as long as you hold the mouse button down. Releasing the mouse button will turn off the relay. Note: You can also use the 1, 2, 3, and 4 keys on your computer’s keyboard to activate the relays. (Use the number keys at the top of the keyboard, not the numeric keypad).

## Overview of the MonsterShield Editor

The Editor window is divided up into the following sections:

1. Menu bar
2. Settings and Animation Slots
3. Command buttons
4. Relay tracks
5. Output window
6. Status bar

In the top left-hand corner of the screen there are 3 tabs labeled Settings, Trigger, and MP3.

### Settings tab

On the settings tab, you can set the playback mode, change the number of slots available, and toggle the ambient playback mode.

#### Slots / Commands:

By default, the MonsterShield is configured for 15 animation slots, and each slot can contain up to 1024 events or commands. Each time a relay changes state, this counts as an event. Because some users may have props where they need more than 1024 events, we offer the ability to reduce the number of slots available while increasing the number of events per slot. The options are shown here:

When you choose a new option, you will get the following confirmation prompt:

If you click OK, the MonsterShield will be reconfigured to the new slots mode and all on-board animation will be erased.

#### Playback mode

There are 4 playback modes to choose from: Sequential (default), single, random, and chain. See the “Using the MonsterShield” section for a description of what these playback modes mean.

If you are connected to a MonsterShield, changing this option will instantly set this option on the MonsterShield.

#### Setting the Ambient playback mode

Clicking on the “Slot 0 Ambient?” checkbox will toggle the ambient playback mode on and off. See the “Using the MonsterShield” section for more information about what this means.

### Trigger tab

This tab contains the settings for customizing how the trigger works on the MonsterShield. If you are connected to the MonsterShield, adjusting these settings will adjust them on the MonsterShield in real-time.

#### Threshold

This setting indicates the minimum voltage that the MonsterShield must see before allowing it to be triggered. Drag the slider to change the value. Note that you must be connected to a MonsterShield for this to have any effect.

#### Sensitivity

This setting is used to smooth out false reads from your trigger. Moving the slider to the left makes it more sensitive and more susceptible to false triggers, and moving the slider to the right makes it less sensitive and less susceptible to false triggers.

#### Cooldown

This setting allows you to specify a delay that must pass before the MonsterShield will be allowed to be triggered again after the last animation has finished playing. This can be set anywhere from 0 seconds to 255 seconds.

#### Trigger on (HIGH or LOW)

This setting allows you to specify whether your prop will trigger when voltage appears above the threshold (HIGH) or when voltage drops below the threshold (LOW). The default setting is HIGH and is what most users will probably use.

#### Ignore new triggers until voltage resets

Checking this box will cause subsequent triggers to be ignored until the voltage resets to the previous state before the prop was first triggered. This will prevent endless triggers if a beam sensor is knocked out of alignment, for example.

### MP3 tab

The MP3 tab lets you select MP3 files from various locations on your computer and assign them to the animation slots. You don’t have to use an MP3 file on every animation slot – it’s up to you. When you save your MonsterShield files, these MP3 locations will be saved with the file. The MonsterShield editor will automatically play the MP3 file through your computer’s sound system for any slot that is assigned an MP3 file with the “Select MP3 files” option when the animation slot is played/triggered. This allows you to hear the sound you have selected even if you haven’t connected audio hardware to the MonsterShield.

#### Select MP3 files

Clicking the “Select MP3 files” button will display the MP3 Files screen:

Click the “…” button next to the slot to show a file explorer that will allow you to choose an MP3 file for that slot:

The MP3 files need not be in the same directory. The MonsterShield Editor will save the locations of any MP3 files selected with the .mos file.

#### Copy MP3 files to SD card

Another feature found in the MP3 tab is the “Copy MP3 files to SD card” button. This feature greatly simplifies getting your MP3 files to your SD card so that they can be used by the MP3 player connected to the MonsterShield. Normally you would have to copy your MP3 files to your SD card yourself and rename each one to “000.mp3”, “001.mp3”, “002.mp3” and so on. Clicking this button will show you the following screen:

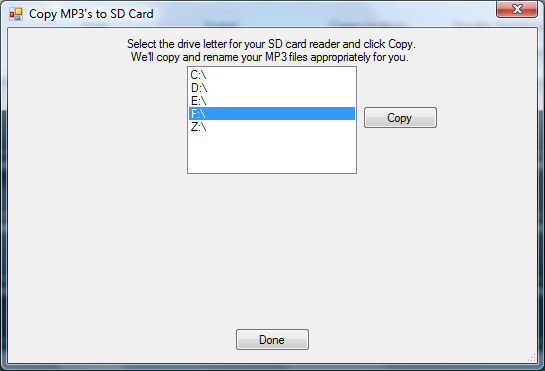
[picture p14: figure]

Simply select the drive letter for your SD card reader and click the “Copy” button:

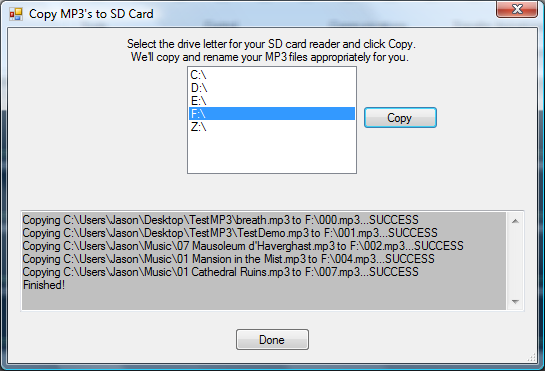
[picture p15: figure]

You will see the status of each copy operation and a “SUCCESS” or “FAILURE” indicator. Now you can take the SD card out of your SD card reader and install it on the MP3 module.

### Animation Slots

This section of the editor shows you a button for each animation slot. Clicking on a button will make that animation slot the currently active animation. Note that if you have a MonsterShield connected, you can cycle through the animation slots from the MonsterShield or from the detachable keypad. You’ll see the appropriate animation slot become selected on the screen for you.

Below each animation slot is a checkbox. This checkbox shows you whether that animation slot is enabled (checked) or disabled (unchecked). Simply click on the checkbox to toggle this in real-time.

### Command Buttons

#### Zoom

##### +

Pressing this button will zoom the relay tracks in 1 level

Pressing this button will zoom the relay tracks out 1 level

#### Tools

##### Edit

While this button is highlighted, you can edit the animation in the relay tracks with the mouse. Using a left click on a track will turn a relay on and a right click will turn the relay off. Hold down the SHIFT key while clicking to edit all 4 tracks at the same time.

##### Select

While this button is highlighted, you can select a portion of the animation window with the left mouse button and do cut, copy, paste, and clear operations (see the Edit menu).

#### Control

##### Trigger/Play

Pressing this button will begin playback of the currently selected animation slot.

##### Stop

Pressing this button will interrupt the playback of the current animation.

#### Communications

##### Connect/Disconnect

Clicking this button will connect or disconnect from your MonsterShield.

#### Transfer Animations

##### Get This

Clicking this button will download the currently selected animation slot from the MonsterShield

##### Send This

Clicking this button will upload the currently selected animation slot to the MonsterShield

##### Get All

Clicking this button will download all animation slots from the MonsterShield

##### Send All

Clicking this button will upload all animation slots to the MonsterShield

## Editing Animations

To edit an animation slot, simply select the Edit button by clicking it, then use the left mouse button and right mouse buttons in the relay tracks. Click and drag to the left or the right to “draw” in the track. Wherever you use the left mouse button will turn ON the relay. This will be shown as a “peak” or plateau. Wherever you use the right mouse button will turn OFF the relay. This will be shown as a valley. Example:

You can draw in all 4 tracks simultaneously by holding down the SHIFT key while drawing with the left mouse button or right mouse button. Example:

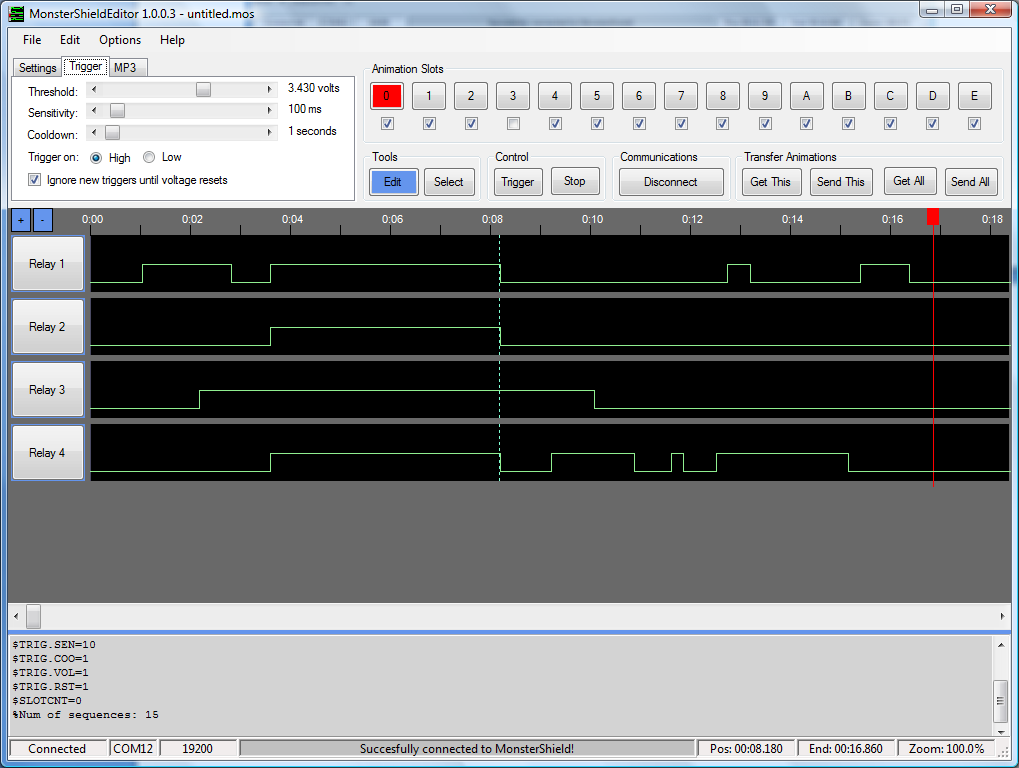
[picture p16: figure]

You can cut, copy, paste, and clear sections of the animation by using the Select tool. Click on the Select tool to select that tool. Clicking on the tracks will allow you draw a selection around the animation:

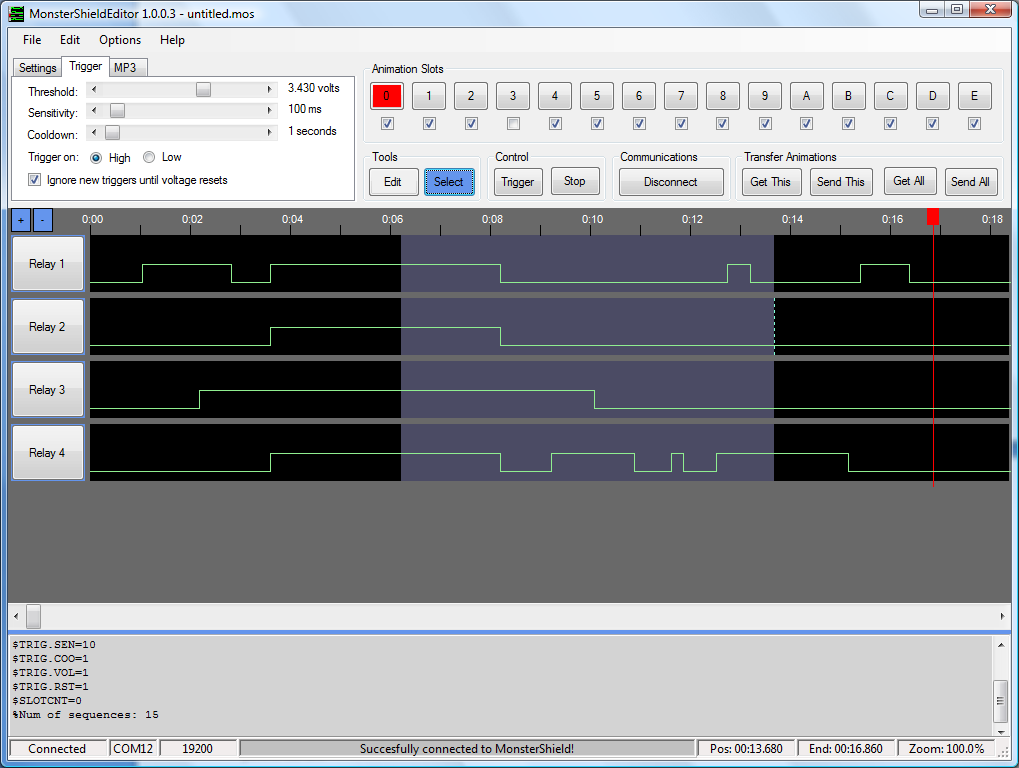
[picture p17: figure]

The Cut, Copy, Paste, and Clear, and Select All options are available in the Edit menu.

# Loading or Updating the Firmware (Arduino code)

If you did not purchase the Arduino from us and are using your own Arduino, you will need to load the code onto the Arduino that makes the MonsterShield work. If you purchased the Arduino from us, it should already have the MonsterShield firmware loaded and you will not have to perform the steps below unless you want to update to the latest firmware.

Note: A good indicator that the MonsterShield firmware is not loaded on your Arduino is if the LED2 light blinks once per second and the single digit display does not illuminate when the MonsterShield is powered on.

Please note that Steps 1 – 3 may have to be performed before using the MonsterShield Editor for the first time, regardless of where you bought your Arduino.

STEP 1: If you have not done so already, please download the latest Arduino software from http://arduino.cc/en/Main/Software.

STEP 2: Unzip the software to a directory and launch the “arduino.exe” file inside the Arduino directory.

STEP 3: Connect a USB cable to the Arduino and your computer. The first time you do this, you may be prompted by Windows to install the drivers for your Arduino. You should point Windows to the “drivers” directory located in the Arduino directory. Windows should find and install the appropriate drivers for your Arduino automatically.

WARNING: IT IS NOT RECOMMENDED TO CONNECT EXTERNAL POWER TO THE ARDUINO WHLE USING THE USB CABLE! DOING SO MAY DAMAGE THE ARDUINO AND/OR THE MONSTERSHIELD!

STEP 4: Launch the Arduino software by double-clicking the “arduino.exe” file in the Arduino directory. You should something like this:

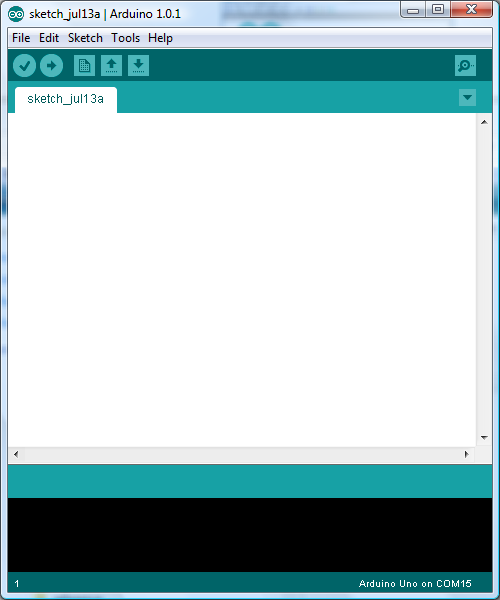
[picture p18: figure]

The first time you launch the Arduino software, you need to specify which type of Arduino you have. You can do this by choosing the correct option under the Tools -> Board menu:

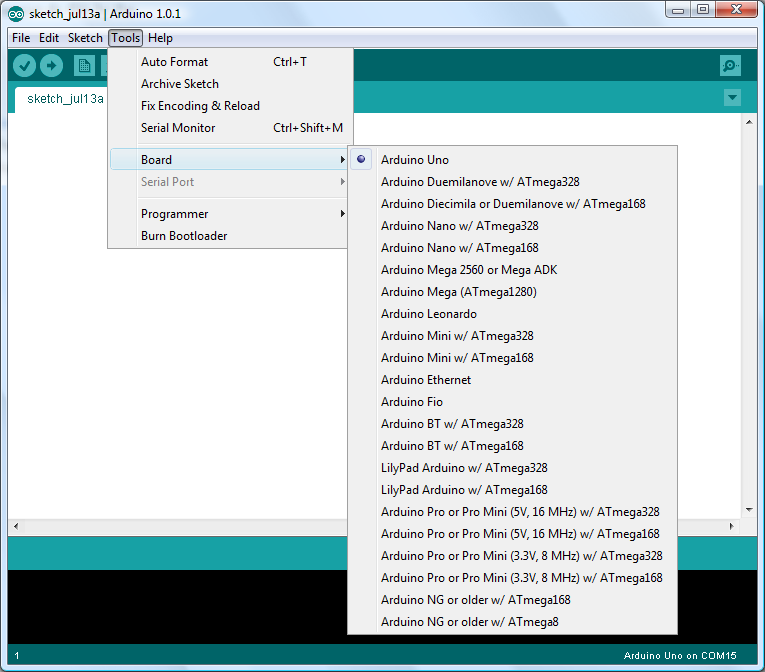
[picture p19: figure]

If your Arduino is connected to a USB cable that is plugged in, you should be able to see at least 1 serial port listed in the Tools -> Serial Port menu.

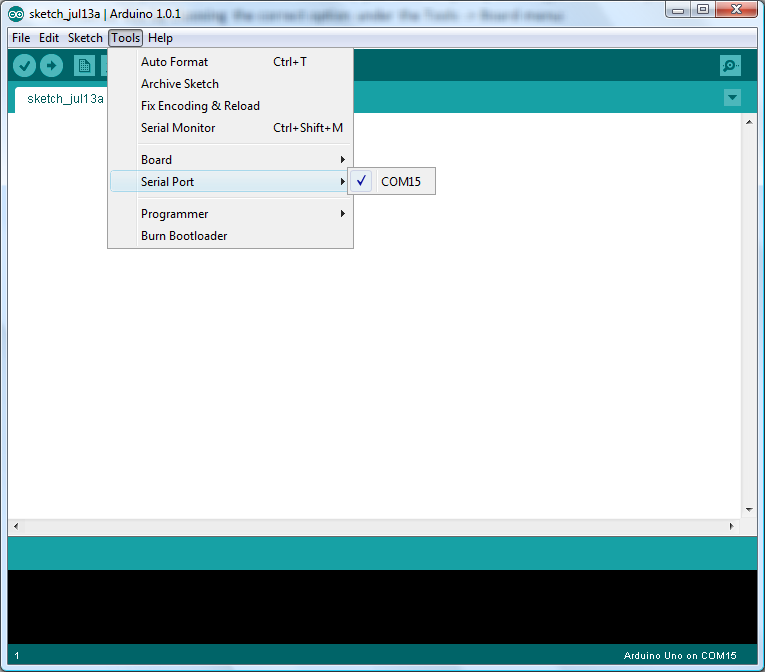
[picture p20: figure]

STEP 5: Download and install the latest MonsterShield software from http://www.hauntsoft.com. Included in the .zip file is the Arduino code for the MonsterShield, which will be named “MonsterShield_Firmware_VXXX.ino” where the “XXX” is the version number.

STEP 6: In the Arduino software, select the File -> Open menu option:

Select the MonsterShield_Firmware_VXXX.ino file and click Open. If you get the following message, just click OK:

The firmware is now loaded into the Arduino software:

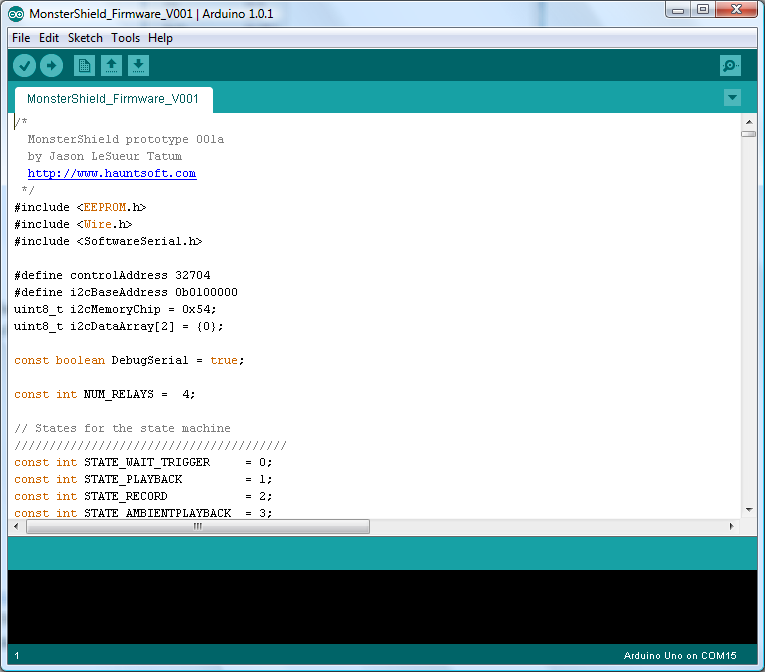
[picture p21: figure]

STEP 7: Now click the second button (a right-facing arrow) as shown here:

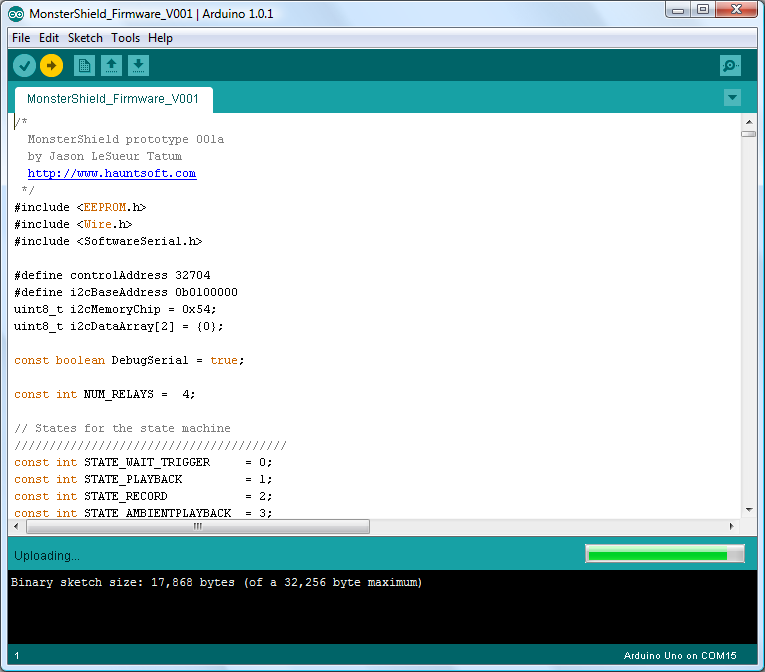
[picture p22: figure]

This will compile and download the MonsterShield code (firmware) to the Arduino. When it is finished, you should see the message “Done uploading” near the bottom of the screen and you should not see any errors listed in the bottom portion of the screen:

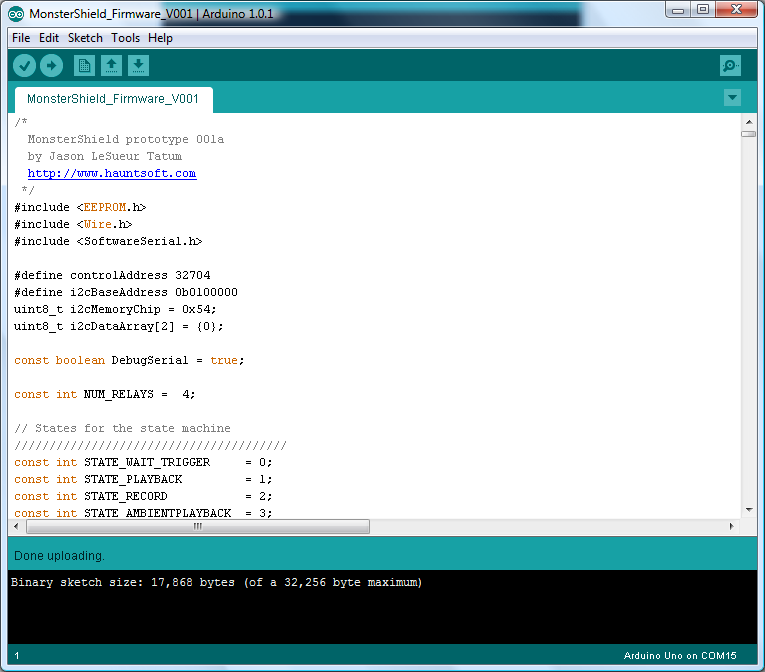
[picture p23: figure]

The MonsterShield should have also initialized and you should see the number “0” being displayed on the single-digit display.

If the Arudino was not connected or there was a problem, you would see something like this:

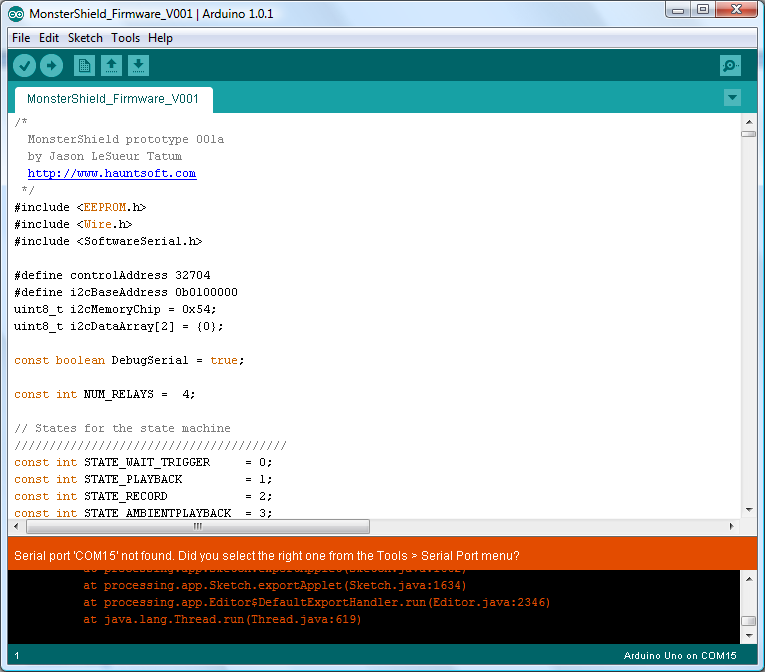
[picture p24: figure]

# Troubleshooting Guide:

Problem: The single digit display does not light up and the LED2 light flashes on & off when the MonsterShield/Arduino is powered up

Solution: The Arduino is missing the MonsterShield code (firmware/sketch). Please see”Loading or Updating Firmware” section of the manual.

Problem: When the MonsterShield is powered on, the number “0” is displayed and LED1 is lit but the MonsterShield does not respond to any button presses.

Solution: The MonsterShield was put in ambient mode without any animation being programmed on slot 0. You have to perform a factory reset on the MonsterShield to reset it to the default settings. Press and hold the “prev/enable” button and press and release the “Reset” button while continuing to hold the “prev/enable” button. After a few seconds the single digit display should begin flashing the letter “F”. Release the “prev/enable” button. The MonsterShield should now operate normally.

Problem: The MonsterShield Editor does not show my Arduino’s com port in the com port menu.

Solution: You plugged in the Arduino after the MonsterShield Editor was already loaded. Simply restart the MonsterShield Editor and you should see your Arduino’s com port.

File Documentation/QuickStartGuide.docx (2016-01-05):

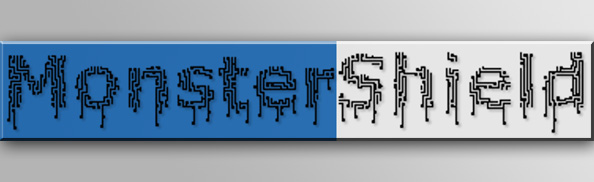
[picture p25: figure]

MonsterShield

Quick Start Guide

8/29/2013

HauntSoft

Jason Tatum

1. Connect MonsterShield to Arduino: Carefully connect the Arduino to the MonsterShield. The MonsterShield has 2 banks of 8 pins and 2 banks of 6 pins on the bottom of the board that are designed to connect to the Arduino. Hold the Arduino in one hand and hold the MonsterShield in the other. Line up the MonsterShield so that the end with MP3 module connector is opposite the end on the Arduino that has the power & USB connectors. Make sure that the right-most pins on the MonsterShield line up with the right-most headers on the Arduino. Make sure the pins are lined up and seat the MonsterShield all the way down. Note that some Arduinos can accept additional pins that the MonsterShield does not have. It should look like this when properly connected:

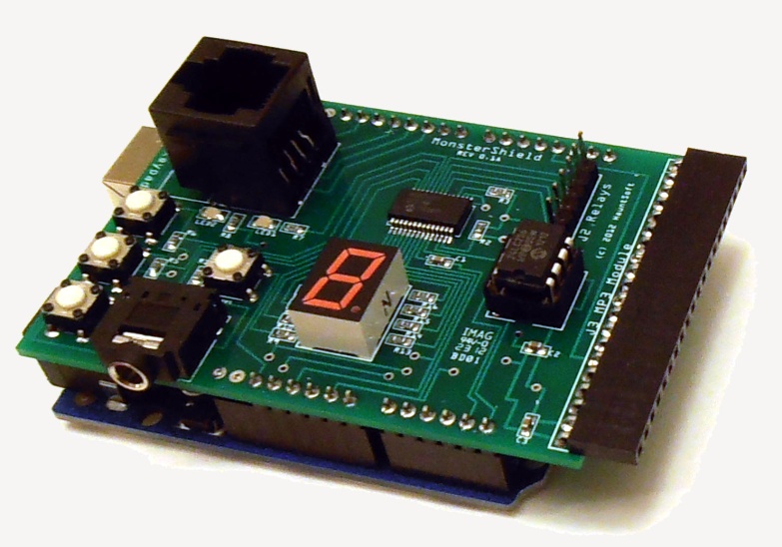
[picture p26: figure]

2. Connect Relay Module to MonsterShield: Connect one end of the included ribbon cable to the J2 6-pin header so that the red wire on the ribbon cable goes to the left-most pin (labeled GND) on the MonsterShield. Insert the other end of the cable to 6-pin header on the relay module so that the red wire is connected to the pin that is labeled GND. If you have a multi-colored cable, just make sure the same color wire is connected to the GND pins on both the MonsterShield and the relay module.

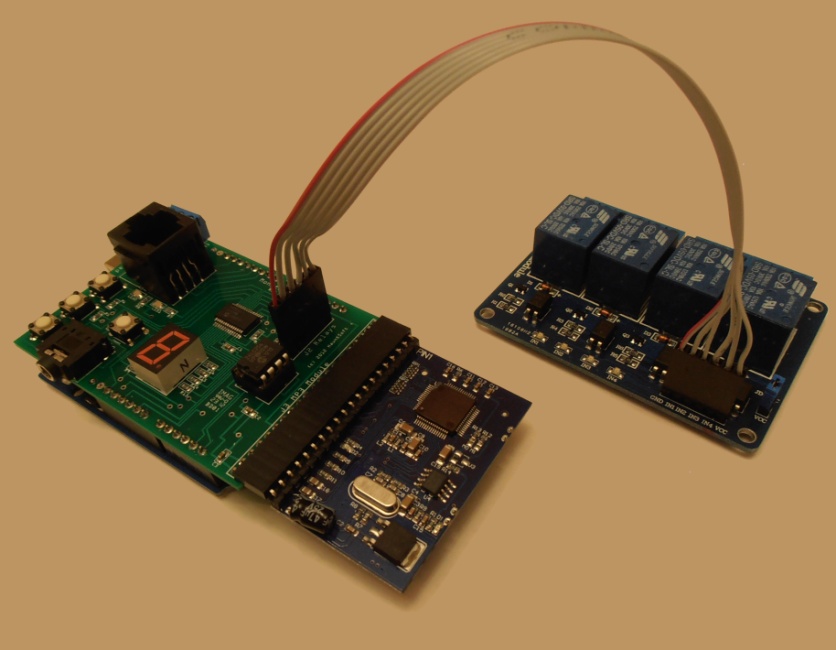
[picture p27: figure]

3. Connecting devices to be controlled by the relays: How you connect devices to the relays depends on what devices you plan to control and what the power requirements are. You can connect devices to be normally closed (power is on normally, but power switches off when relay is turned on) or normally open (power is off normally, but power switches on when relay is turned on). Here are some common ways to connect devices to the relay module:

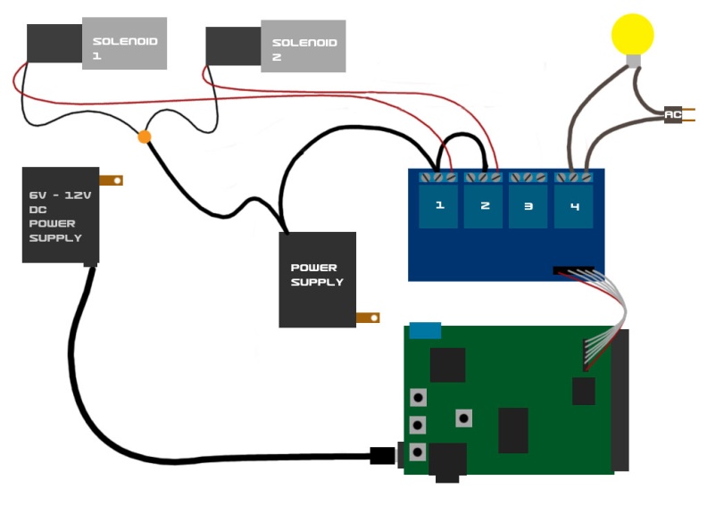
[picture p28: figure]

4. Connect Trigger: Connect a trigger (such as a motion sensor, push button, or beam sensor) to the J1 blue screw terminals on the MonsterShield. The screw terminals are labeled as +5V, Trigger, and GND. Note that some trigger types only require the +5 and the Trigger terminals (such as a beam sensor or a push button). Triggers that require +5V to operate will use all 3 terminals (such as the Parallax PIR motion sensor). If your trigger has different power requirements (such as a beam sensor that requires 12V), you will need to connect a separate power supply to the trigger (or if it is a 12V trigger you can use the 12V 2A power supply and the splitter cable to provide power to the trigger) and you use the +5V and the Trigger terminals on the switched leads for the trigger. For example, the Fright Props beam sensor has 5 wires. Two wires supply 12V power to the sensor. The other 3 wires are common, normally open, and normally closed. You would use only the common and normally open or the common and normally closed (but not all 3 at the same time), and these would be wired to the +5V and the Trigger terminals, but it doesn’t matter which wire goes to which of the terminals.


5. Connect Optional MP3 module: If you purchased the optional MP3 module, connect it to the J3 MP3 Module header on the MonsterShield so that the SD card slot is on the bottom. Note that it is easier to install and remove the SD card from the MP3 module with the MP3 module removed from the MonsterShield. Copy MP3 files to your SD card and name them 000.mp3 through 014.mp3. The 3 digit number corresponds to the animation slot it will be played with.

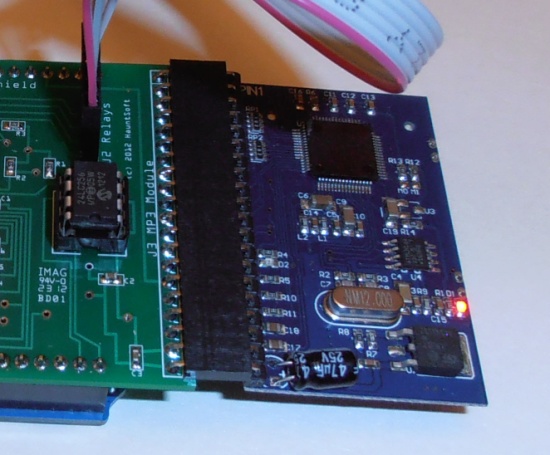
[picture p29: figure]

Connect a 1/8” stereo jack to the MonsterShield and connect this to a powered amplifier or speaker system. Note that the output from this jack is headphone level, which means it is pre-amplified for headphones. This may cause damage or distortion to sensitive equipment that is not designed to handle this level. This can be addressed by using a small adapter cable that has a built-in volume control. Adjust the volume until the distortion disappears.

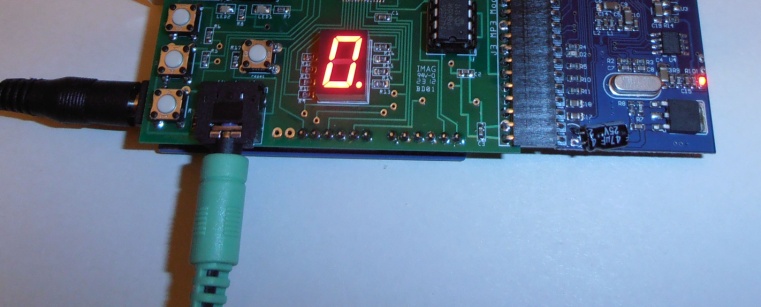
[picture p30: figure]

6. Connect Power to Arduino: Connect your power source (6V DC to 12V DC) to the Arduino. If you are using the 12V 2A power supply and the optional splitter cable, connect the splitter cable between the power supply and the Arduino. Make sure that the bare leads on the other end of the cable are not touching each other. The MonsterShield will power up and should display “-“ for a second or two. It may also flash “F” for a few seconds, which indicates it is performing an automatic factory reset. When complete, the MonsterShield should display a “0”. If the single digit display does NOT display any digit and LED2 is flashing on and off, then this means you have not loaded the MonsterShield code onto the Arduino. You will need to download the firmware from http://www.hauntsoft.com/downloads and you will need to install it using the Arduino IDE (which can be obtained from http://www.arduino.cc).
7. Using the optional keypad: Attach the optional keypad using a standard cat5 network cable. When connected, the keypad has two modes: Normal & Record.
  a. In Normal mode, you can cycle through all the animation slots by using the first 2 buttons (next and previous). The 3rd button acts as a toggle for enabling or disabling the currently selected animation slot. The 4th button manually triggers the prop. Pressing the 4th button while an animation is running will stop the animation.
  b. Pressing the 5th button will prepare the MonsterShield to record animation on the currently selected slot. See the Recording Animation below.

Now test your animation by pressing the play button.

8. Manually triggering your prop: Press the “mode/trigger” button on the MonsterShield or the “play/stop” button on the keypad to manually trigger your prop. Pressing these buttons again will interrupt and stop the animation from playing.
9. Selecting an animation slot: Press and release the “prev/enable” button or the “next/ambient” buttons on the MonsterShield repeatedly to cycle through the animation slots. Don’t hold these buttons down because this activates their secondary functions. You can also press the “Prev” and “Next” buttons on the keypad to cycle through the animations.
10. Recording an animation: Select the animation slot you wish to record and press the Record button on the keypad. You will first be prompted to make 3 selections:
  a. Bank Selection: First the MonsterShield will begin flashing the letter “b” on the display. This is the bank selection prompt. Press the Out 1 button to select bank 0 on the MonsterShield. If you have a MonsterShield Expander board connected, you could also press Out 2, Out 3, or Out 4 to select banks 1, 2, or 3. The selected bank number will begin flashing. Press and release the record button to confirm the selected bank. Note: If you do not have a MonsterShield Expander board attached, you could skip this and just press the record button and bank 0 will be selected automatically.
  b. Relay Selection: Now the MonsterShield will begin flashing the letter “r” on the display. This is the relay selection prompt that allows you to select which relay output / track you want to record animation to. If you would like to record animation on all relays for the selected bank, just press the record button again. If you would like to only record animation for a single relay on the bank (and ignore inputs on the other relays), then select the relay you want to program by pressing Out 1, Out 2, Out 3, or Out 4. Press the record button to confirm the relay selection.
  c. Record Mode: Now the MonsterShield will begin flashing the letter “c” on the display. This is the recording mode prompt. There are 3 options:
    i. Mode 0: Overlay – This lays down animation on top of what was already previously recorded. If you had previously recorded events on the selected relay/tracks but want to record addition events on the same track, you can use this option. During recording, previous events on these relays/tracks will be played while allowing you record new events on top.
    ii. Mode 1: Wipe selected relay track – This clears all previous animation from the selected relays/tracks but keeps the animation data for all the other relays/tracks.
    iii. Mode 2: Wipe entire animation – This clears all of the animation for all banks and all relays letting you start from scratch for this animation.

Press Out 1, Out 2, or Out 3 to select the recording mode you desire. Then press the Record button to begin recording the animation.

The letter “P” will begin flashing on the display to indicate you are now in Record Program mode. Press and release the Out 1, Out 2, Out 3, and Out 4 buttons to turn the relay outputs on and off as desired. When finished recording, press the Record button again.

11. Disabling or Enabling an animation slot: Select the animation slot you want to enable or disable. You can tell if an animation slot is enabled or disabled by the decimal point on the single digit display. If a slot is enabled, the decimal point will be lit. To toggle the slot between enabled & disabled, simply press and hold the “prev/enable” button on the MonsterShield for 1 second and then release. You can also press the “enable” button on the keypad to toggle the slot.
12. Setting Playback mode: There are currently 3 playback modes: Sequential, Single, & Random. You can cycle between the playback modes by pressing and holding the “mode/trigger” button on the MonsterShield for more than 1 second and releasing. The MonsterShield will flash “P” and “1”, “2”, or “3”. “1” means sequential mode (the default). Each time the prop is triggered, the MonsterShield will advance to the next slot after the animation has finished playing. “2” means random mode. Each time the prop is triggered, the MonsterShield will randomly select which animation to play. “3” means single mode. The MonsterShield will stay on this slot every time it is triggered. If Ambient mode is turned on, then slot 0 will never be selected when the prop is triggered.
13. Ambient mode: Ambient Mode turns animation slot 0 into an ambient animation that plays in a continuous loop. When the prop is triggered, the slot 0 animation is interrupted and the triggered animation plays. When the triggered animation is finished, the MonsterShield will go back to playing animation slot 0 in a continuous loop. You can toggle the ambient animation on & off by pressing and holding the “nxt/ambient” button on the MonsterShield for more than 1 second and releasing. WARNING: Make SURE you have recorded an animation on slot 0 before turning ambient mode on. If you forget to do this, the MonsterShield could go into an endless loop that cannot be interrupted. You will have to perform a factory reset which will initialize all settings to the defaults and will wipe out all animation on the MonsterShield. If the letter “E” flashes for several seconds when you attempt to turn on Ambient mode, it means the MonsterShield detected no animation on slot 0 and aborted the Ambient mode.
14. Performing a Factory Reset: If you need to perform a factory reset, press and hold the “prev/enable” button on the MonsterShield and then press and release the “reset” button while continuing to hold the “prev/enable” button. The MonsterShield will reset and begin performing a factory reset to the defaults. When the letter “F” begins rapidly flashing, you may release the “prev/enable” button. After a few seconds, the MonsterShield will begin flashing “F” once a second. This is prompting you to confirm how many animation slots you want to configure on the MonsterShield. Your options are 1, 2, 3, 4, 5, 6, 7, 8, 9, A (10), B (11), C (12), D (13), E (14), and F (15). F is the default. You can cycle through the available selections using the “prev/enable” and “nxt/ambient” buttons. To confirm your selection, press the “mode/trigger” button. If no user selection is made after 10 seconds, then the MonsterShield will configure itself to the default of 15 slots. Generally speaking, the fewer slots you configure the MonsterShield for, the longer each animation can be.
15. Connecting to your computer: Before you can begin using the MonsterShield with your computer, you will have to install the Arduino drivers. These drivers are included and automatically installed with the MonsterShield software version 1.0.0.4 and later. The drivers are also available by downloading the Arduino IDE:
  a. Download the Arduino IDE from http://www.arduino.cc and unzip it to your computer.
  b. Connect the MonsterShield to your computer using a standard USB printer cable. Windows will detect that a new piece of hardware has been added. You will need to tell Windows to look in the Arduino directory’s “drivers” subdirectory.
  c. Windows should then find and install the appropriate driver for your Arduino.

SPECIAL NOTES IF YOU HAVE THE MONSTERSHIELD EXPANDER BOARD:

1. Connect additional relay modules to the headers marked bank 1, bank 2, and bank 3. Bank 0 is the relay bank on the main MonsterShield board itself. Bank 4 can only be utilized by writing your own custom code.
2. The MonsterShield Expander should be seated between the Arduino and the MonsterShield.
3. You can populate 0, 1, or 2 additional EEPROM chips on the MonsterShield Expander board. Currently only the 24LC256 chip is supported, but we will be adding support for larger chips in the future. You must install the chip(s) (if not already installed) with the notch facing the power-side of the Arduino.
4. There are 2 additional removable terminal blocks on the Expander board. The block facing the power side of the Arduino is used to provide external 5V power to additional relay modules. If you are using more than 1 relay module, you must connect a 5V 1A (high amperage is okay) to the 5V and GND terminals on this terminal block. DO NOT connect more than 5V or you will damage the relay circuits! It is recommended that you power the main MonsterShield before powering the expander board. This prevents all the additional relays from turning on during power up.

For further information, please review the full manual which can be obtained from http://www.hauntsoft.com/downloads.aspx or by installing the MonsterShield Editor software.

Quick Start GuidePage 6

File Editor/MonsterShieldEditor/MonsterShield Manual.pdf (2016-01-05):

# MonsterShield

## User Manual

8/27/2012
Copyright © 2012 by HauntSoft Written by Jason LeSueur Tatum

2 MonsterShield

### Contents

### Specifications & Features

- Modular components allow replacement of relay module, EEPROM, Arduino, and MP3 player
- Controls up to 4 devices with the 4 relay module
- Each relay rated for both AC and DC current.
- Each relay supports up to 10 amps at 125VAC and 10 amps at 30VDC.
- All animations and settings are stored on a user-replaceable non-volatile 32 kilobyte EEPROM chip.
- Supports up to 15 separate animations
- Each animation can be up to 16 minutes long
- Animation slots can be toggled as enabled or disabled with a push of a button on either the MonsterShield or with the detachable keypad.
- Animations can be manually triggered right from the MonsterShield or from the detachable keypad
- Detachable keypad connects using a standard network cable allowing you to stand in front of your prop while you program it
- Detachable keypad allows you to use 1 keypad with multiple MonsterShield-controlled props.
- Animations can be programmed by hand using the optional detachable keypad programmer, or they can be programmed visually using the powerful MonsterShield Editor software and a Windows computer.
- Optional MP3 module with SD card support for up to 8GB SD cards
- 4 different playback modes: sequential, single, random, and chain (chain not yet implemented)
- Ambient animation mode allows animation slot 0 to repeat continuously while waiting for a trigger
- Trigger supports voltages between 0.4 volts and 5 volts DC. Minimum trigger threshold can be configured in the MonsterShield Editor.
- Trigger can be configured to trigger on LOW voltage or HIGH voltage.
- Trigger can be configured to ignore repeated triggers if the input voltage has not returned to its un-triggered state. This prevents endless triggering if a beam sensor is knocked out of alignment with its reflector.
- Trigger supports a “cool down” feature that prevents frequent triggers. This can be set between 0 to 255 seconds.
- Trigger supports an adjustable sensitivity setting to help eliminate false triggers. This can be configured in increments of 10 milliseconds up to 2550 milliseconds.
- MonsterShield has a built-in serial interface that allows developers to write their own software to control the MonsterShield while connected to a computer via the USB port. You can use the MonsterShield for other applications, such as home automation!
- MonsterShield Editor allows you to download all animations to and from the MonsterShield. You can save the animations to a file for backup.

- MonsterShield hardware can be hacked to add additional features. There are several unused pins from the Arduino that you could utilize for your own purposes. The RJ-45 connector also has an unused digital I/O pin and there are +5 and GND pins on the connector as well.
- The MonsterShield code (Arduino sketch) that runs on the Arduino is available for you to look at and modify with purchase of the MonsterShield.

### Using the MonsterShield

### Getting Started

The MonsterShield prop controller consists of 3 major components:

- MonsterShield board
- Arduino
- Relay module

In addition to these 3 major components, there are optional components are available:

- MP3 module
- Detachable programming keypad

Items not shown:

- External power supply
- Ethernet cable (not included, used with the detachable keypad)
- USB cable (optional)

### Quick Start Guide

1. Connect MonsterShield to Arduino: Carefully connect the Arduino to the MonsterShield. The MonsterShield has 2 banks of 8 pins and 2 banks of 6 pins on the bottom of the board that are designed to connect to the Arduino. Hold the Arduino in one hand and hold the MonsterShield in the other. Line up the MonsterShield so that the end with MP3 module connector is opposite the end on the Arduino that has the power & USB connectors. Make sure that the right-most pins on the MonsterShield line up with the right-most headers on the Arduino. Make sure the pins are lined up and seat the MonsterShield all the way down. Note that some Arduinos can accept additional pins that the MonsterShield does not have. It should look like this when properly connected:
2. Connect Relay Module to MonsterShield: Connect one end of the included ribbon cable to the J2 6-pin header so that the red wire on the ribbon cable goes to the left-most pin (labeled GND) on the MonsterShield. Insert the other end of the cable to 6-pin header on the relay module so that the red wire is connected to the pin that is labeled GND.

3. Connecting devices to be controlled by the relays: How you connect devices to the relays depends on what devices you plan to control and what the power requirements are. You can connect devices to be normally closed (power is on normally, but power switches off when relay is turned on) or normally open (power is off normally, but power switches on when relay is turned on). Here are some common ways to connect devices to the relay module:

MonsterShield and Four 12V solenoid valves powered with 12V 2A power supply

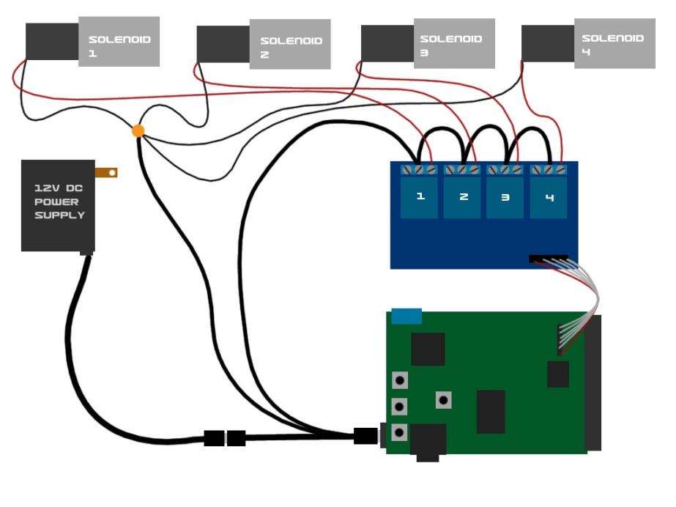
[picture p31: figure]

MonsterShield and solenoid valves powered separately

### 2 solenoid valves powered separate and 1 AC output

4. Connect Trigger: Connect a trigger (such as a motion sensor, push button, or beam sensor) to the J1 blue screw terminals on the MonsterShield. The screw terminals are labeled as +5V, Trigger, and GND. Note that some trigger types only require the +5 and the Trigger terminals (such as a beam sensor or a push button). Triggers that require +5V to operate will use all 3 terminals (such as the Parallax PIR motion sensor). If your trigger has different power requirements (such as a beam sensor that requires 12V), you will need to connect a separate power supply to the trigger (or if it is a 12V trigger you can use the 12V 2A power supply and the splitter cable to provide power to the trigger) and you use the +5V and the Trigger terminals on the switched leads for the trigger. For example, the Fright Props beam sensor has 5 wires. Two wires supply 12V power to the sensor. The other 3 wires are common, normally open, and normally closed. You would use only the common and normally open or the common and normally closed (but not all 3 at the same time), and these would be wired to the +5V and the Trigger terminals, but it doesn’t matter which wire goes to which of the terminals.

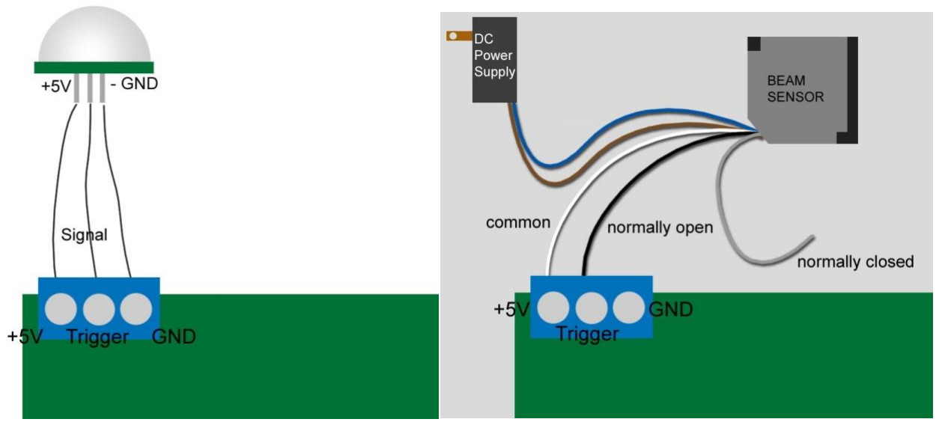
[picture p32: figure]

5. Connect Optional MP3 module: If you purchased the optional MP3 module, connect it to the J3 MP3 Module header on the MonsterShield so that the SD card slot is on the bottom. Note that it is easier to install and remove the SD card from the MP3 module with the MP3 module removed from the MonsterShield. Copy MP3 files to your SD card and name them 000.mp3 through 014.mp3. The 3 digit number corresponds to the animation slot it will be played with.

Connect a 1/8” stereo jack to the MonsterShield and connect this to a powered amplifier or speaker system. Note that the output from this jack is headphone level, which means it is pre-amplified for headphones. This may cause damage or distortion to sensitive equipment that is not designed to handle this level. This can be addressed by using a small adapter cable that has a built-in volume control. Adjust the volume until the distortion disappears.

6. Connect Power to Arduino: Connect your power source (6V DC to 12V DC) to the Arduino. If you are using the 12V 2A power supply and the optional splitter cable, connect the splitter cable between the power supply and the Arduino. Make sure that the bare leads on the other end of the cable are not touching each other. The MonsterShield will power up and should display “-“ for a second or two. It may also flash “F” for a few seconds, which indicates it is performing an automatic factory reset. When complete, the MonsterShield should display a “0”. If the single digit display does NOT display any digit and LED2 is flashing on and off, then this means you have not loaded the MonsterShield code onto the Arduino. You will need to download the firmware from http://www.hauntsoft.com/downloads and you will need to install it using the Arduino IDE (which can be obtained from http://www.arduino.cc).
7. Using the optional keypad: Attach the optional keypad using a standard cat5 network cable. When connected, the keypad has two modes: Normal & Record.
a. In Normal mode, you can cycle through all the animation slots by using the first 2 buttons (next and previous). The 3rd button acts as a toggle for enabling or disabling the currently selected animation slot. The 4th button manually triggers the prop. Pressing the 4th button while an animation is running will stop the animation.
b. Pressing the 5th button will put the MonsterShield in record mode. The currently selected animation slot will begin flashing on the single digit display. Press the first 4 buttons to turn the relay outputs on and off as desired. When finished recording, press the record button again. Now test your animation by pressing the play button.
8. Manually triggering your prop: Press the “mode/trigger” button on the MonsterShield or the “play/stop” button on the keypad to manually trigger your prop.
9. Selecting an animation slot: Press the “prev/enable” button or the “next/ambient” buttons on the MonsterShield repeatedly to cycle through the animation slots. Don’t hold these buttons down because this activates their secondary functions.
10. Recording an animation: Select the animation slot you wish to record and press the record button the keypad. The selected slot number will begin flashing indicating you are in record mode. Begin pressing the 4 output buttons as desired to control the 4 relay outputs. When finished recording, press the record button.
11. Disabling or Enabling an animation slot: Select the animation slot you want to enable or disable. You can tell if an animation slot is enabled or disabled by the decimal point on the single digit display. If a slot is enabled, the decimal point will be lit. To toggle the slot between enabled & disabled, simply press and hold the “prev/enable” button on the MonsterShield for 1 second and then release. You can also press the “enable” button on the keypad to toggle the slot.
12. Setting Playback mode: There are currently 3 playback modes: Sequential, Single, & Random. You can cycle between the playback modes by pressing and holding the “mode/trigger” button on the MonsterShield for more than 1 second and releasing. The MonsterShield will flash “P” and “1”, “2”, or “3”. “1” means sequential mode (the default). Each time the prop is triggered, the MonsterShield will advance to the next slot after the animation has finished playing. “2” means single mode. The MonsterShield will stay on this slot every time it is triggered. “3” means random mode. Each time the prop is triggered, the MonsterShield will randomly select which animation to play. If Ambient mode is turned on, then slot 0 will never be selected when the prop is triggered.
13. Ambient mode: Ambient Mode turns animation slot 0 into an ambient animation that plays in a continuous loop. When the prop is triggered, the slot 0 animation is interrupted and the triggered animation plays. When the triggered animation is finished, the MonsterShield will go back to playing animation slot 0 in a continuous loop. You can toggle the ambient animation on & off by pressing and holding the “nxt/ambient” button on the MonsterShield for more than 1 second and releasing. WARNING: Make SURE you have recorded an animation on slot 0 before turning ambient mode on. If you forget to do this, the MonsterShield will go into an endless loop that cannot be interrupted. You will have to perform a factory reset which will initialize all settings to the defaults and will wipe out all animation on the MonsterShield.
14. Performing a Factory Reset: If you need to perform a factory reset, press and hold the “prev/enable” button on the MonsterShield and then press and release the “reset” button while continuing to hold the “prev/enable” button. The MonsterShield will reset and begin performing a factory reset to the defaults. When the letter “F” begins rapidly flashing, you may release the “prev/enable” button. When the flashing stops the MonsterShield should be on slot
0. The Factory Reset is now complete.

15. Connecting to your computer: Before you can begin using the MonsterShield with your computer, you will have to install the Arduino drivers. Download the Arduino IDE from http://www.arduino.cc and unzip it to your computer. Connect the MonsterShield to your computer using a standard USB printer cable. Windows will detect that a new piece of hardware has been added. You will need to tell Windows to look in the Arduino directory’s “drivers” subdirectory. Windows should then find and install the appropriate driver for your Arduino. For further information on using the MonsterShield with your computer and with the MonsterShield Editor, please consult the full manual after installing the MonsterShield Editor software from http://www.hauntsoft.com/downloads.

### Connecting Modules & Cables

Attaching MonsterShield to an Arduino
The first step is to connect the MonsterShield board to an appropriate Arduino (such as the Arduino UNO R3). Please note that the MonsterShield will not function without an Arduino.

The MonsterShield has 2 banks of 6 male pins and 2 banks of 8 male pins on the bottom of the board for plugging into an Arduino. Some Arduinos (such as the Arduino UNO R3) have 2 additional pin positions on both of the leftmost female headers that are not used by the MonsterShield. When connecting the MonsterShield to an Arduino, make sure that the rightmost pins on the MonsterShield match up with the rightmost female pin sockets on the Arduino. Push the MonsterShield all the way down so that it is seated snug on top of the Arduino. This is what the MonsterShield should look like after attaching to the Arduino:

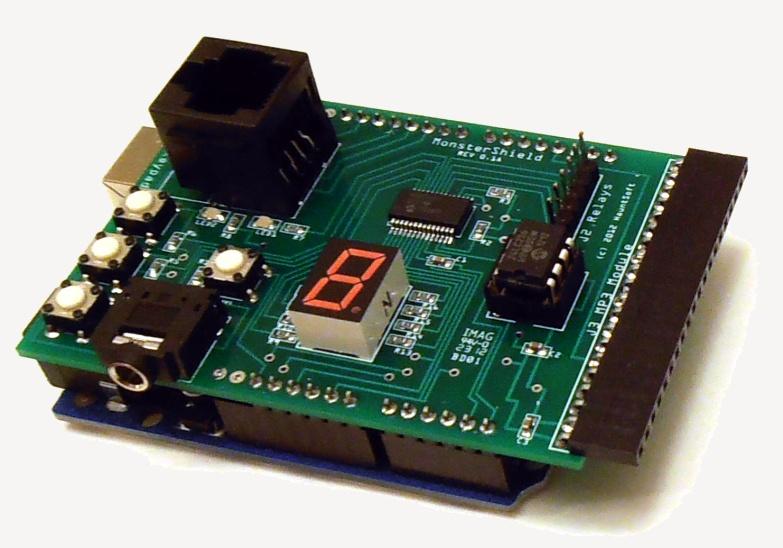
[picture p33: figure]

Connecting the Relay module to the MonsterShield
Connect the Relay Module to the MonsterShield using the supplied 6-pin ribbon cable.
STEP 1: Connect one end of the cable to the 6-pin male connector labeled “J2 Relays” on the MonsterShield, ensuring that the red wire is towards the left of the “J2 Relays” label.
STEP 2: Connect the other end of the cable to the 6-pin male connector on the relay module ensuring that the red wire is on the pin labeled “GND”.

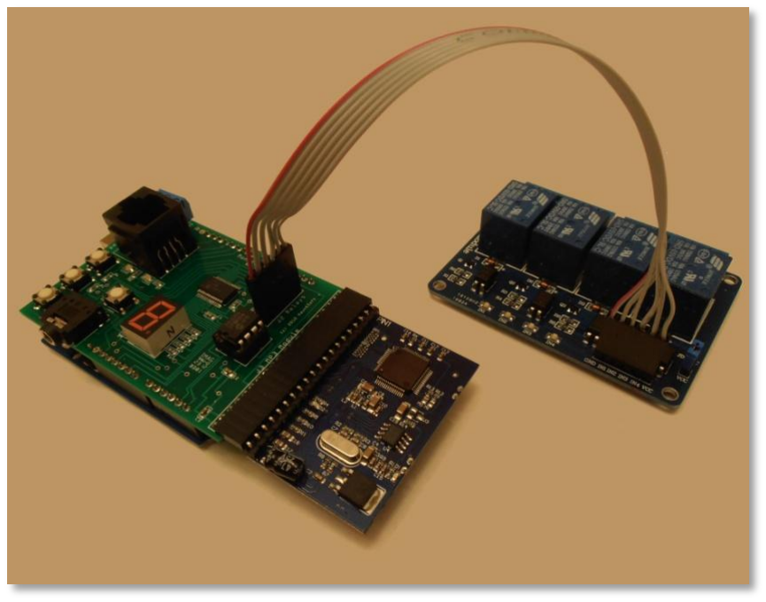
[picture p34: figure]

WARNING: IMPROPERLY CONNECTING THIS CABLE CAN DAMAGE YOUR MONSTERSHIELD AND/OR ARDUINO!

Connecting the MP3 module (optional) to the MonsterShield
If you purchased the MP3 module, you can connect that to the MonsterShield now. Do not connect or disconnect the MP3 module while the MonsterShield is powered on.

Insert the MP3 module into the 20-pin female connector on the right edge of the MonsterShield. The SD card should be on the bottom of the MP3 player when connecting the MP3 module. Note that it is easier to install and remove the SD card from the MP3 player when the MP3 player is removed from the MonsterShield.

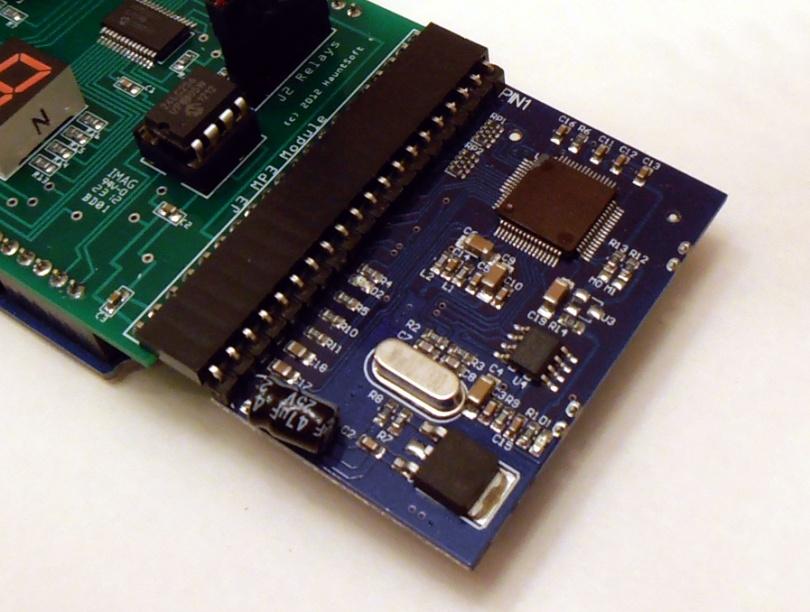
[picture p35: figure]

The MP3 module will not do anything without an SD card loaded with MP3 files. Before using the MP3 module, you should load MP3 files onto a standard 1GB, 2GB, 4GB, or 8GB SD card. In order for the MP3 player to work properly, you need to rename your MP3 files in the following way:

000.mp3 | Slot 0
001.mp3 | Slot 1
002.mp3 | Slot 2
003.mp3 | Slot 3
004.mp3 | Slot 4
005.mp3 | Slot 5
006.mp3 | Slot 6
007.mp3 | Slot 7
008.mp3 | Slot 8
009.mp3 | Slot 9
010.mp3 | Slot A (10)
011.mp3 | Slot B (11)
012.mp3 | Slot C (12)
013.mp3 | Slot D (13)
014.mp3 | Slot E (14)

As an example, whenever animation slot 5 is activated, the corresponding 005.mp3 file will be played. You do not have to have every file. Missing files simply means there won’t be any sound for those particular animation slots.

Note that you can also use the MonsterShield Editor on a Windows OS computer to simplify this task. The MonsterShield Editor has a “MP3” tab. On this tab, there is a button to select your MP3 files and another button to copy all of the chosen files to your SD card reader. The software will take care of renaming the files on the SD card for you.

Connecting Audio
The MonsterShield has a 3.5mm stereo jack for audio out. Connect your amplifier or amplified speakers to this jack. Note that the output from this jack is slightly amplified for headphone use. Because of this, some amplifiers may be distorted from too strong a signal. If you experience this, the distortion can be eliminated by using a cable with a volume control on it. Adjust the volume knob on the cable until the distortion is removed.

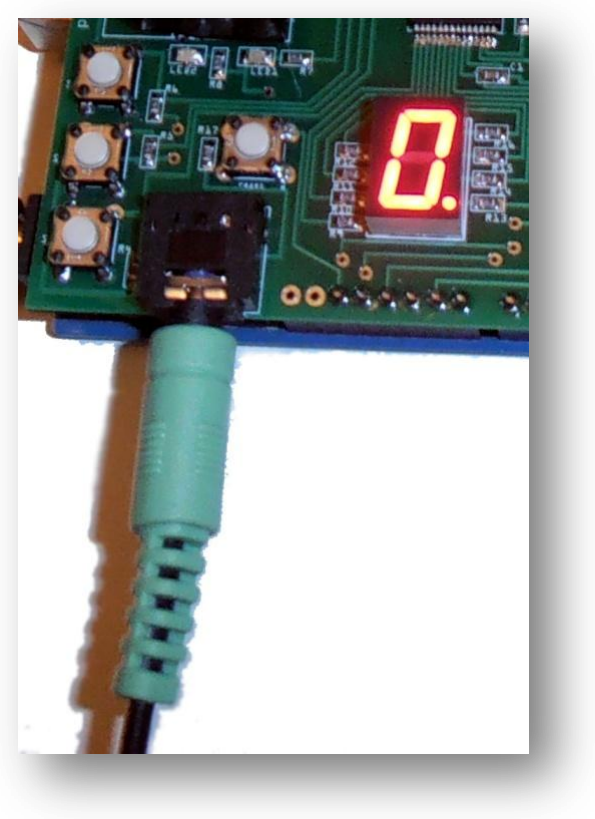
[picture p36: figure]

Connecting a Trigger
There are 3 screw terminals housed in a blue connector labeled “J1 Trigger”. This is for connecting a trigger to the MonsterShield, such as a push button, motion sensor, pressure mat, etc. The 3 terminals are labeled as:

+5V

TRIGGER

GND

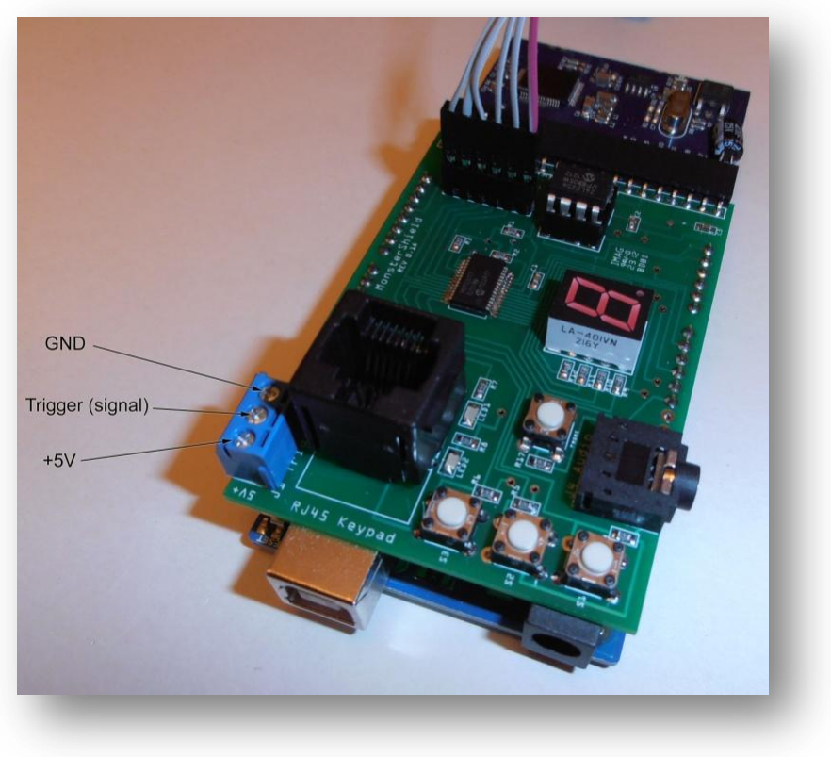
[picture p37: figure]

By default, in order to trigger the prop, the TRIGGER terminal will need to see between 3V and 5V. You can adjust the minimum voltage threshold using the MonsterShield Editor. You can test the trigger by simply using a jumper wire and touching the +5V terminal and the TRIGGER terminal at the same time.

How to connect a push button trigger:
A push button trigger normally requires 2 wires. Connect 1 wire to the +5V and the other wire to the TRIGGER. Pressing the button “closes” the circuit and causes the prop to be triggered.

How to connect a motion sensor:
Check your motion sensor and see what its power requirements are and make sure the signal wire for the motion sensor does not output more than 5V. WARNING: The Arduino and/or MonsterShield may be damaged if you send more than 5V to the TRIGGER terminal! A motion sensor that works well is the Parallax motion sensor. This motion sensor has 3 pins labeled +, signal, -. Connect the motion sensor the MonsterShield trigger via a cable. Connect the + to the +5V screw terminal on the MonsterShield trigger and the – to the GND screw terminal on the MonsterShield trigger, and connect the signal to the TRIGGER screw terminal on the MonsterShield.

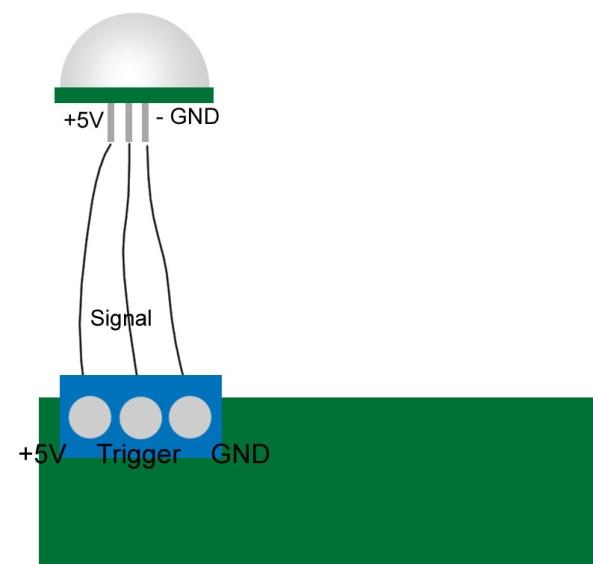
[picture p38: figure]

How to connect a beam sensor:
A beam sensor usually requires separate power and can’t be powered from the +5V connection on the MonsterShield. If your beam sensor works with 12V, you can use the 12V 2A power supply and splitter cable sold by HauntSoft to power your beam sensor. Beam sensors usually work like a light switches and merely complete the circuit on 2 wires when the beam is broken. Most beam sensors will have 5 wires, and you’ll likely only need to use 4 of them. 2 wires are for powering the beam sensor, and 2 wires are for connecting the output. One of the output wires will be the “common” wire and the other output wire you will use will be either the “normally open” wire or the “normally closed” wire. Which wire you use depends on how you want to use the beam sensor and how you configure the trigger on the MonsterShield. If you use the “normally open” wire, electricity will flow between the common wire and the normally open wire only when the beam is broken. You should set the trigger mode to “HIGH” in the MonsterShield Editor (this is also the factory default). If you want to use “normally closed”, then electricity flows between the common and the normally closed wire until the beam is broken, at which point electricity stops flowing. You will need to set the trigger mode to “LOW” in the MonsterShield Editor.

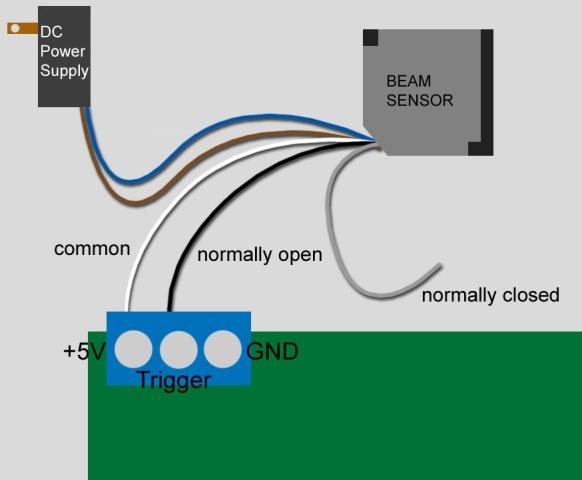
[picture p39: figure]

How to connect a pressure mat sensor:
A pressure mat normally requires 2 wires. Connect 1 wire to the +5V and the other wire to the TRIGGER. Applying pressure to the mat “closes” the circuit and causes the prop to be triggered.

Connecting Power
Connect an external power supply with a barrel-style connector to the Arduino. The power supply should be rated for 6V – 12V DC and at least 650 mA. We recommend the 12V 2A power supply if you intend to power 12V solenoid valves and/or 12V sensors from the same power supply that is providing power to the MonsterShield.

Note: When connecting the MonsterShield to your computer, you can disconnect the external power supply from the Arduino although this is not necessary. The Arduino will get its power from the USB cable. Also note that you may hear some static on the audio from the MP3 module on the MonsterShield when the relays are being switched on and off while the MonsterShield is being powered by the USB cable. This is because the USB cable does not provide enough power to operate the MP3 player without distortion. This distortion should go away when powered externally with a sufficient power supply.

Connecting devices to the relays
The relay module is where you will connect the devices that will be controlled by the MonsterShield. The relays on the relay module are rated for up to 30VDC at 10 amps and 125VAC at 10 amps. This will allow you to control just about anything. Examples include:
- Solenoid valves for pneumatics (12V or 24V are the most common)
- AC or DC lights
- AC or DC motors
- Fog machine triggers
- Flood lights

WARNING: Please use CAUTION when controlling AC current with the MonsterShield. There is risk of shock or electrocution when controlling AC current with the relays. Never come into contact with any part of the relay module when powered by AC current.

WARNING: Please be aware that the current controlled by the relays is external to the MonsterShield and there could be live current going to the relays even with the MonsterShield unplugged. Because of this, assume that there is always a shock hazard or risk of electrocution even when the MonsterShield is unpowered!

Devices can be connected to the Relays on the Relay modules in two ways. You can connect a device so that it is normally closed (current flows until when the relay is turned off and current stops when the relay is turned on) or you can connect a device so that it is normally open (current only flows when the relay is turned on).

For most devices, you will connect only 2 wires to a relay.

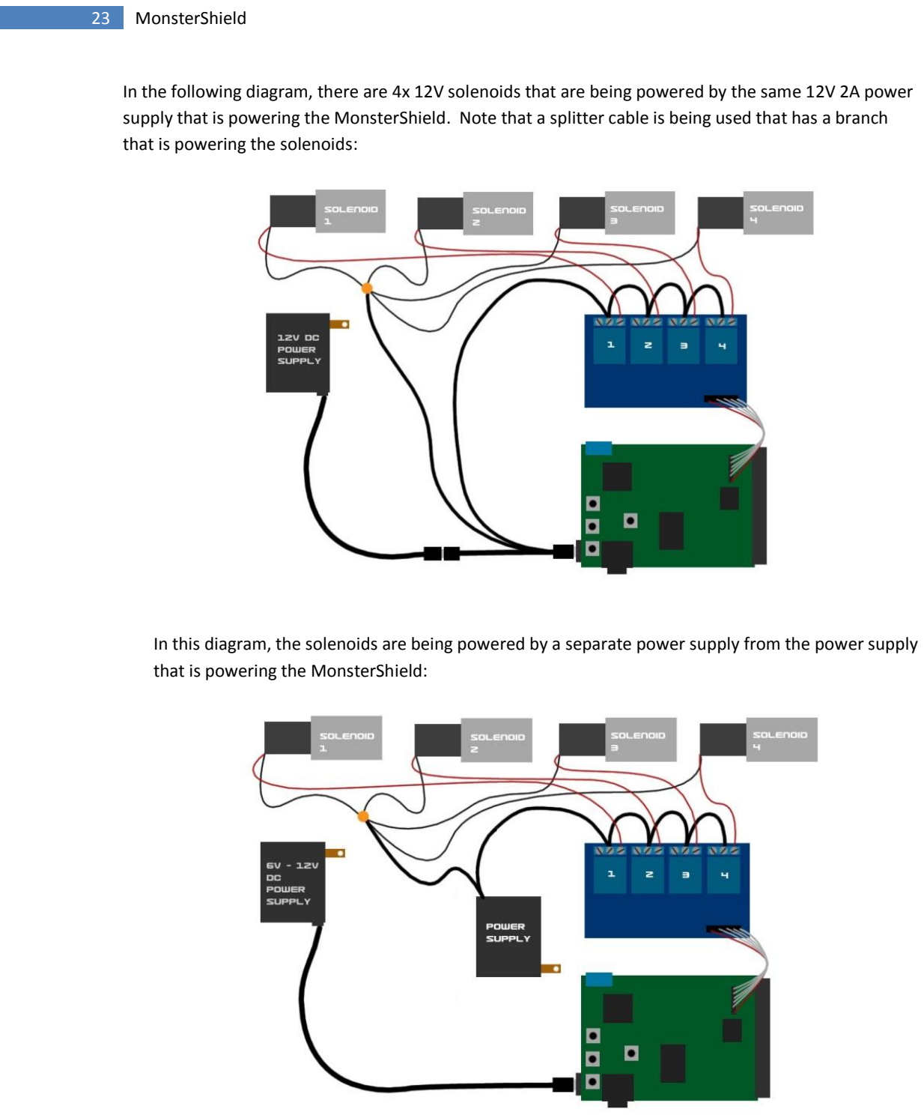
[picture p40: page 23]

In the following diagram, there are 4x 12V solenoids that are being powered by the same 12V 2A power supply that is powering the MonsterShield. Note that a splitter cable is being used that has a branch that is powering the solenoids:

In this diagram, the solenoids are being powered by a separate power supply from the power supply that is powering the MonsterShield:

Finally, in this diagram, 2 solenoids are being powered by a separate power supply and 1 AC light is being powered by an AC plug. Please use extreme caution when connecting AC lines to the relay module!


### Using the MonsterShield

Using the on-board buttons
There are 3 multi-purpose buttons on the MonsterShield plus a reset button. The following is a brief description of each button and its uses:

MODE / TRIGGER
Pressing this button will manually trigger the MonsterShield to begin playing an animation.

Pressing and holding this button for at least 1 second and releasing (long-pressing) will cycle through the next playback mode. The MonsterShield has the following playback modes:

1 | Sequential – Each time prop is triggered, MonsterShield advances to the next enabled slot after the animation has finished playing.
2 | Single – Each time prop is triggered, the currently selected animation slot plays.
3 | Random – Each time prop is triggered, the MonsterShield will randomly select the next animation slot to play the next time it is triggered.
4 | Chain (NOT YET IMPLEMENTED) – Plays each enabled animation slot one after the other as if they were 1 giant animation.

Each time this button is long-pressed, the MonsterShield will advance to the next playback mode and will flash the number shown in the left column of the table above for the currently selected playback mode for several seconds.

PREV / ENABLE
Pressing this button will select the previous animation slot. If the MonsterShield was currently on animation slot 5, pressing this button will make slot 4 the current slot, and the number “4” will be shown on the single digit display.

Long-pressing this button will toggle whether the currently selected animation slot is enabled or disabled. A disabled animation slot will never be played by the MonsterShield. You can tell if an animation slot is enabled or disabled by the decimal point on the bottom right corner of the single digit display. If the decimal point is lit, then the currently selected animation slot is enabled. If the decimal point is not lit, then the currently selected animation slot is disabled.

NXT / AMBIENT
Pressing this button will advance to the next animation slot. If the MonsterShield was currently on animation slot 5, then pressing this button will advance to animation slot 6 and the number “6” will be shown on the single digit display.

Long-pressing this button will toggle Ambient mode on & off. When Ambient mode is on, the MonsterShield will play animation slot 0 in a continuous loop without being triggered. Once the prop is triggered, then the MonsterShield will stop playing animation slot 0 and will begin playing one of the other animation slots (1 through E) as appropriate for the currently selected playback mode. Once that animation has finished playing, the MonsterShield will go back to playing animation slot 0 in a continuous loop. When ambient mode is turned on, the left green LED on the MonsterShield will flash continuously twice per second. Long-pressing this button again will turn off ambient mode and animation slot 0 will stop playing.

RESET
Should the MonsterShield ever lock-up or behave erratically, pressing this button will reset the Arduino / MonsterShield. Sometimes when connecting an external power supply, the Arduino needs to be reset once. You can tell if you need to do this if the single digit display does not light up after a couple of seconds.

PERFORMING A FACTORY RESET
If you need to perform a factory reset, press and hold the “prev/enable” button on the MonsterShield and then press and release the “reset” button while continuing to hold the “prev/enable” button. The MonsterShield will reset and begin performing a factory reset to the defaults. When the letter “F” begins rapidly flashing, you may release the “prev/enable” button. When the flashing stops the MonsterShield should be on slot 0. The Factory Reset is now complete.

Using the optional keypad


To use the optional keypad, simply attach a standard Cat5 or Cat6 network cable between the keypad and the MonsterShield. The keypad and the MonsterShield both have RJ-45 connectors for this purpose. You can use any length of network cable up to 25 feet. We have not tested network cables longer than 25 feet, but they might still work. Note that you do not need to power off the MonsterShield when attaching or detaching the keypad. It is designed for this purpose so that you can quickly detach it from MonsterShield and connect it to another MonsterShield without having to shut off the power.

The keypad has two modes: Normal mode & Record mode.

Normal Mode
When the MonsterShield is not in record mode, it is in Normal Mode. When in Normal Mode, the keypad has several useful functions. You can cycle through all of the animation slots using the Previous slot and next slot buttons. You can toggle whether an animation slot is enabled or disabled by pressing the enable/disable button. You can manually trigger a prop animation to play by pressing the Manual Trigger button. You can also force an animation to stop playing by holding down the Manual trigger button for more than 1 second and releasing.

Record Mode
You enter Record Mode by pressing the Record button. The currently selected animation slot shown on the single digit display will begin flashing and the associated MP3 file will start playing (if MP3 module is present and associated file exists on the SD card). You can start activating the relays by pressing the 4 input buttons. Holding a button down will keep the relay on until the button is released. The MonsterShield will accurately record every input you do along with the actual timings. When you are finished recording the animation simply press the Record button a second time. This animation is now stored on the MonsterShield’s EEPROM memory chip and will be saved even if you remove power from the MonsterShield.

### MonsterShield Editor Software

The MonsterShield Editor software is available for download from the http://www.hauntsoft.com

This software allows you to access the advance features of the MonsterShield and allows you to visually see and edit all of the animations on the MonsterShield. You can download previously recorded animations from the MonsterShield, or upload new animations that you’ve created using the editor. You can also backup all your animations to a file for safe keeping.

### Installing the software

Download the MonsterShield Editor from http://www.hauntsoft.com and install on a Windows XP, Windows Vista, or Windows 7 computer. Run the setup program and follow the on-screen prompts.

The first time you launch the MonsterShield Editor, you may be asked to enter your registration code. This should have been emailed to you when you placed your order.

### Launching the MonsterShield Editor

Double-click the MonsterShield Editor icon after installing the software. When you first launch the editor, this is what you will see:

While it is not necessary to have the MonsterShield connected to your computer when you launch the editor, it is recommended. Adjusting settings on-screen will adjust them on the MonsterShield in real-time if the MonsterShield is connected.

Select the COM port for your MonsterShield by going to the Options -> Com Port menu and selecting the appropriate com port for you MonsterShield:

Click the Connect button to connect to your MonsterShield. You should see the message “Successfully connected to the MonsterShield” in the status bar. If the software failed to connect to your MonsterShield, you will see a red error message in the status bar. Example:


After you have successfully connected to the MonsterShield, you can test the relays simply by clicking on the 4 Relay buttons on the left side of the screen. You should see the appropriate indicator light flash on the relay module. Press and hold the left mouse button will keep the relay on for as long as you hold the mouse button down. Releasing the mouse button will turn off the relay. Note: You can also use the 1, 2, 3, and 4 keys on your computer’s keyboard to activate the relays. (Use the number keys at the top of the keyboard, not the numeric keypad).

### Overview of the MonsterShield Editor

The Editor window is divided up into the following sections:

1. Menu bar
2. Settings and Animation Slots
3. Command buttons
4. Relay tracks

5. Output window
6. Status bar

In the top left-hand corner of the screen there are 3 tabs labeled Settings, Trigger, and MP3.

Settings tab
On the settings tab, you can set the playback mode, change the number of slots available, and toggle the ambient playback mode.

Slots / Commands:

By default, the MonsterShield is configured for 15 animation slots, and each slot can contain up to 1024 events or commands. Each time a relay changes state, this counts as an event. Because some users may have props where they need more than 1024 events, we offer the ability to reduce the number of slots available while increasing the number of events per slot. The options are shown here:

When you choose a new option, you will get the following confirmation prompt:

If you click OK, the MonsterShield will be reconfigured to the new slots mode and all on-board animation will be erased.

Playback mode
There are 4 playback modes to choose from: Sequential (default), single, random, and chain. See the “Using the MonsterShield” section for a description of what these playback modes mean.

If you are connected to a MonsterShield, changing this option will instantly set this option on the MonsterShield.

Setting the Ambient playback mode
Clicking on the “Slot 0 Ambient?” checkbox will toggle the ambient playback mode on and off. See the “Using the MonsterShield” section for more information about what this means.

Trigger tab
This tab contains the settings for customizing how the trigger works on the MonsterShield. If you are connected to the MonsterShield, adjusting these settings will adjust them on the MonsterShield in real-time.

Threshold

This setting indicates the minimum voltage that the MonsterShield must see before allowing it to be triggered. Drag the slider to change the value. Note that you must be connected to a MonsterShield for this to have any effect.

Sensitivity
This setting is used to smooth out false reads from your trigger. Moving the slider to the left makes it more sensitive and more susceptible to false triggers, and moving the slider to the right makes it less sensitive and less susceptible to false triggers.

Cooldown
This setting allows you to specify a delay that must pass before the MonsterShield will be allowed to be triggered again after the last animation has finished playing. This can be set anywhere from 0 seconds to 255 seconds.

Trigger on (HIGH or LOW)
This setting allows you to specify whether your prop will trigger when voltage appears above the threshold (HIGH) or when voltage drops below the threshold (LOW). The default setting is HIGH and is what most users will probably use.

Ignore new triggers until voltage resets
Checking this box will cause subsequent triggers to be ignored until the voltage resets to the previous state before the prop was first triggered. This will prevent endless triggers if a beam sensor is knocked out of alignment, for example.

MP3 tab
The MP3 tab lets you select MP3 files from various locations on your computer and assign them to the animation slots. You don’t have to use an MP3 file on every animation slot – it’s up to you. When you save your MonsterShield files, these MP3 locations will be saved with the file. The MonsterShield editor will automatically play the MP3 file through your computer’s sound system for any slot that is assigned an MP3 file with the “Select MP3 files” option when the animation slot is played/triggered. This allows you to hear the sound you have selected even if you haven’t connected audio hardware to the MonsterShield.

Select MP3 files

Clicking the “Select MP3 files” button will display the MP3 Files screen:

Click the “…” button next to the slot to show a file explorer that will allow you to choose an MP3 file for that slot:

The MP3 files need not be in the same directory. The MonsterShield Editor will save the locations of any MP3 files selected with the .mos file.

Copy MP3 files to SD card
Another feature found in the MP3 tab is the “Copy MP3 files to SD card” button. This feature greatly simplifies getting your MP3 files to your SD card so that they can be used by the MP3 player connected to the MonsterShield. Normally you would have to copy your MP3 files to your SD card yourself and rename each one to “000.mp3”, “001.mp3”, “002.mp3” and so on. Clicking this button will show you the following screen:


Simply select the drive letter for your SD card reader and click the “Copy” button:


You will see the status of each copy operation and a “SUCCESS” or “FAILURE” indicator. Now you can take the SD card out of your SD card reader and install it on the MP3 module.

Animation Slots
This section of the editor shows you a button for each animation slot. Clicking on a button will make that animation slot the currently active animation. Note that if you have a MonsterShield connected, you can cycle through the animation slots from the MonsterShield or from the detachable keypad. You’ll see the appropriate animation slot become selected on the screen for you.

Below each animation slot is a checkbox. This checkbox shows you whether that animation slot is enabled (checked) or disabled (unchecked). Simply click on the checkbox to toggle this in real-time.

Command Buttons

Zoom

+
Pressing this button will zoom the relay tracks in 1 level
Pressing this button will zoom the relay tracks out 1 level

Tools

Edit
While this button is highlighted, you can edit the animation in the relay tracks with the mouse. Using a left click on a track will turn a relay on and a right click will turn the relay off. Hold down the SHIFT key while clicking to edit all 4 tracks at the same time.

Select
While this button is highlighted, you can select a portion of the animation window with the left mouse button and do cut, copy, paste, and clear operations (see the Edit menu).

Control

Trigger/Play
Pressing this button will begin playback of the currently selected animation slot.

Stop
Pressing this button will interrupt the playback of the current animation.

Communications

Connect/Disconnect
Clicking this button will connect or disconnect from your MonsterShield.

Transfer Animations

Get This
Clicking this button will download the currently selected animation slot from the MonsterShield

Send This
Clicking this button will upload the currently selected animation slot to the MonsterShield

Get All
Clicking this button will download all animation slots from the MonsterShield

Send All
Clicking this button will upload all animation slots to the MonsterShield

### Editing Animations

To edit an animation slot, simply select the Edit button by clicking it, then use the left mouse button and right mouse buttons in the relay tracks. Click and drag to the left or the right to “draw” in the track. Wherever you use the left mouse button will turn ON the relay. This will be shown as a “peak” or plateau. Wherever you use the right mouse button will turn OFF the relay. This will be shown as a valley. Example:

You can draw in all 4 tracks simultaneously by holding down the SHIFT key while drawing with the left mouse button or right mouse button. Example:


You can cut, copy, paste, and clear sections of the animation by using the Select tool. Click on the Select tool to select that tool. Clicking on the tracks will allow you draw a selection around the animation:


The Cut, Copy, Paste, and Clear, and Select All options are available in the Edit menu.

### Loading or Updating the Firmware (Arduino code)

If you did not purchase the Arduino from us and are using your own Arduino, you will need to load the code onto the Arduino that makes the MonsterShield work. If you purchased the Arduino from us, it should already have the MonsterShield firmware loaded and you will not have to perform the steps below unless you want to update to the latest firmware.

Note: A good indicator that the MonsterShield firmware is not loaded on your Arduino is if the LED2 light blinks once per second and the single digit display does not illuminate when the MonsterShield is powered on.

Please note that Steps 1 – 3 may have to be performed before using the MonsterShield Editor for the first time, regardless of where you bought your Arduino.

STEP 1: If you have not done so already, please download the latest Arduino software from http://arduino.cc/en/Main/Software.


STEP 2: Unzip the software to a directory and launch the “arduino.exe” file inside the Arduino directory.
STEP 3: Connect a USB cable to the Arduino and your computer. The first time you do this, you may be prompted by Windows to install the drivers for your Arduino. You should point Windows to the “drivers” directory located in the Arduino directory. Windows should find and install the appropriate drivers for your Arduino automatically.

WARNING: DO NOT CONNECT EXTERNAL POWER TO THE ARDUINO WHLE USING THE USB CABLE! DOING SO MAY DAMAGE THE ARDUINO AND/OR THE MONSTERSHIELD!

STEP 4: Launch the Arduino software by double-clicking the “arduino.exe” file in the Arduino directory. You should something like this:


The first time you launch the Arduino software, you need to specify which type of Arduino you have. You can do this by choosing the correct option under the Tools -> Board menu:

If your Arduino is connected to a USB cable that is plugged in, you should be able to see at least 1 serial port listed in the Tools -> Serial Port menu.


STEP 5: Download and install the latest MonsterShield software from http://www.hauntsoft.com. Included in the .zip file is the Arduino code for the MonsterShield, which will be named “MonsterShield_Firmware_VXXX.ino” where the “XXX” is the version number.
STEP 6: In the Arduino software, select the File -> Open menu option:


Select the MonsterShield_Firmware_VXXX.ino file and click Open. If you get the following message, just click OK:

The firmware is now loaded into the Arduino software:


STEP 7: Now click the second button (a right-facing arrow) as shown here:


This will compile and download the MonsterShield code (firmware) to the Arduino. When it is finished, you should see the message “Done uploading” near the bottom of the screen and you should not see any errors listed in the bottom portion of the screen:

The MonsterShield should have also initialized and you should see the number “0” being displayed on the single-digit display.

If the Arudino was not connected or there was a problem, you would see something like this:


### Troubleshooting Guide:

Problem: The single digit display does not light up and the LED2 light flashes on & off when the MonsterShield/Arduino is powered up

Solution: The Arduino is missing the MonsterShield code (firmware/sketch). Please see”Loading or Updating Firmware” section of the manual.

Problem: When the MonsterShield is powered on, the number “0” is displayed and LED1 is lit but the MonsterShield does not respond to any button presses.

Solution: The MonsterShield was put in ambient mode without any animation being programmed on slot 0. You have to perform a factory reset on the MonsterShield to reset it to the default settings. Press and hold the “prev/enable” button and press and release the “Reset” button while continuing to hold the “prev/enable” button. After a few seconds the single digit display should begin flashing the letter “F”. Release the “prev/enable” button. The MonsterShield should now operate normally.

Problem: The MonsterShield Editor does not show my Arduino’s com port in the com port menu.

Solution: You plugged in the Arduino after the MonsterShield Editor was already loaded. Simply restart the MonsterShield Editor and you should see your Arduino’s com port.

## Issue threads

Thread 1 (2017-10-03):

Editor crashes when MonsterShield becomes connected

kacole2, 2017-10-03:
Hey Jason! How's it going? It's been a while but was hoping you could answer this whenever you get around to it. If you don't recall, I was the one who created the [MonsterRemote](https://github.com/kacole2/monster_remote) based on your genius here. I'm sorry that this project didn't go much further. It had such great potential. I wish I could have taken it over for you but I ended up selling the house that hosted my haunt and moved. I gifted the MonserShield and the bulk of my yard haunt to my neighbors to continue the tradition.

I was over there tonight and I ran into all kinds of problems (including this issue) but was able to work through most of it. The fact that they lost their animation file made it *that* much harder!

Anyway, I know there has to be something I'm overlooking but it's happening on 2 different laptops, one that includes my XP Virtual Machine. I can fire up the MonsterShield Editor, edit tracks, add music, change animations, etc. However, whenever I hit the `connect` button to talk through the COM/USB interface, the Editor program crashes. The weird part is that I can move the crash window over and continue working on the editor, however it's very laggy and can't be certain it's working correctly. I was successfully able to change 1 of the animations that needed to be done. After some more troubleshooting, we got the MonsterShield with MonsterRemote up and running  and setting off props again!

At this point, they aren't in a good situation to ever create new tracks but wanted to see if this crash is related to some driver needed or Visual Studio dll that's missing. I ran this on both XP and Windows 10 and the same error occurred. This is not a critical issue because they don't plan on changing any animations this year but wanted to submit this bug in case anyone else is having the issue.

Hope all is well
Kenny

Xpendable172, 2017-10-03:
Yes, I of course remember you and the awesome MonsterRemote you had
created, as well as your Halloween light show. As you obviously know, I am
no longer involved with the MonsterShield. I am probably not going to be of
much help, but here is what I know... The serial communications (through
the USB / COM) interface can be touchy with the editor. Make sure you
select the right com port. If you select the wrong one I can guarantee it
will likely crash. If your cable is at all flaky or if Windows removes the
com port, you will likely crash. I did experience random crashes out in the
field when working on the Pumpkin Farm and would have to unplug the USB
cable, reset the MonsterShield (not a factory reset, just a quick tap on
reset button), then plug it in then start the editor. Make sure you give
enough time for the com port to reappear. Always always always save your
sequences before attempting to send them. Also recommend saving into
different filenames by adding a version number so you can go back if
something goes wrong along the way. Good luck. Sorry I can't be more help.

Sincerely,
Jason

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

kacole2, 2017-10-03:
@Xpendable172 thanks for the quick response! Two machines, same issue. So it's not the COM port because the window shows serial input/output happening during the connection phase. I'll have to try the cable unplug/tap reset/plug-in next time I'm around.

I figured you weren't maintaining any more but wanted to let you know your creation is still alive and kicking on the biggest halloween street in Louisville, KY.

After sending this message I've spent the entire time seeing if anyone has created a similar board/software combo that has feature parity for the cost... guess what? nothing! Looks like a lot of people have gone the route of Christmas light controllers. I've spent 15 minutes reading up on Falcon and still haven't been able to tell if it could give me what I would have needed. I don't even do crazy halloween stuff anymore but just got sucked into it again. I really miss it during this time of the year. Take care!

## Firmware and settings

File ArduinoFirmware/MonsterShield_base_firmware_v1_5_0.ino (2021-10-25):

/**    
	MonsterShield Prop Controller Editor software
    Copyright (C) 2015  Jason LeSueur Tatum

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
    You should have received a copy of the GNU General Public License
    along with this program.  If not, see <http://www.gnu.org/licenses/>.
**/
#include <EEPROM.h>
#include <Wire.h>
#include <SoftwareSerial.h>

#include "MonsterShield.h"
//#include <Adafruit_PWMServoDriver.h>

MonsterShield monster;


//Adafruit_PWMServoDriver pwm = Adafruit_PWMServoDriver();
//#define SERVOMIN  300 // this is the 'minimum' pulse length count (out of 4096)
//#define SERVOMAX  500 // this is the 'maximum' pulse length count (out of 4096)



void setup()
{
  Serial.begin(115200);    // Used for host computer communication  
  monster.init();


  //pwm.begin();
  //pwm.setPWMFreq(60);  // Analog servos run at ~60 Hz updates
  

}

void loop()
{
  
  boolean wasTriggered = (monster.isTriggerSensed(0) && !monster.ignoreTriggers); // JTATUM 10/24/2021 Added ignoreTriggers to disable trigging if we've disabled the triggers.  Manual triggering still works. 
  boolean modeButton = monster.inputButtonPress(0);
  boolean triggeredFromAmbient = false;
  
  monster.processSerialPort(); // Allow for upload / download of animation and other events to automatically be handled.
  
  ///////////////////////////////////////////
  // If Ambient mode is turned on 
  ///////////////////////////////////////////
  if (monster.getPlayAmbient() == true)
  {
    // Play animation!  Parameters:  slot, repeat, ambient, bit mask for triggers, bit mask for input buttons, bit mask for keypad buttons
    int rc = monster.playAnimationWithInterrupts(0, true, true, 0x01, 0xFF, 0x08);
    if (rc == MONSTERSHIELD_INT_BUTTON_2)
    {
        monster.setPlayAmbient(false);
        triggeredFromAmbient = false;
    }
    else
    {
      monster.playAnimationWithInterrupts(monster.getActiveSlot(), false, false, 0x00, 0x01, 0x08);
    }
  }
  else
  {
  
  
    ////////////////////////////////////////////////////////////
    // Check for Manual playback from MonsterShield button 0 or keypad play button
    ////////////////////////////////////////////////////////////
    if (modeButton == HIGH || monster.keypadButtonPress(MONSTERSHIELD_KEYPAD_PLAY) == HIGH || wasTriggered == true || triggeredFromAmbient == true)
    {
      if (modeButton == HIGH && monster.inputButtonPressLength(0) > 500)
      {
        // Change playback modes
        monster.setNextAnimationSelectMode();
      }
      else
      {
        // Play animation!  Parameters:  slot, repeat, bit mask for triggers, bit mask for input buttons, bit mask for keypad buttons
        //Serial.println("@T0"); //Uncomment to make a slave MonsterShield play along!
        monster.playAnimationWithInterrupts(monster.getActiveSlot(), false, false, 0x00, 0x01, 0x08);
      }
    }
    //////////////////////////////////////////////////////////////
    // Check for previous slot button press or long press to toggle enable
    /////////////////////////////////////////////////////////////
    else if (monster.inputButtonPress(1) == HIGH || monster.keypadButtonPress(MONSTERSHIELD_KEYPAD_PREV) == HIGH)
    {
      if (monster.inputButtonPressLength(1) > 350)
      {
        int slot = monster.getActiveSlot();
        bool enabled = monster.getSlotEnabled(slot);
        monster.setSlotEnabled(slot, !enabled);
        
        monster.setDigitToActiveSlot();
      }
      else
      {
          monster.setPreviousSlot();
      }
    }
  
    //////////////////////////////////////////////////////////////
    // Check for next slot button press
    //////////////////////////////////////////////////////////////
    else if (monster.inputButtonPress(2) == HIGH)
    {
      if (monster.inputButtonPressLength(2) > 500)
      {
        monster.setPlayAmbient(true);
      }
      else
      {
        monster.setNextSlot();
      }
    }
    else if (monster.keypadButtonPress(MONSTERSHIELD_KEYPAD_NEXT) == HIGH)
    {
      monster.setNextSlot();
    }
    
    /////////////////////////////////////////////////
    // Check for toggle of slot enable from keypad
    ////////////////////////////////////////////////
    else if (monster.keypadButtonPress(MONSTERSHIELD_KEYPAD_ENABLE) == HIGH)
    {
      int slot = monster.getActiveSlot();
      bool enabled = monster.getSlotEnabled(slot);
      monster.setSlotEnabled(slot, !enabled);
      monster.setDigitToActiveSlot();
    }
  
    ///////////////////////////////////////////////////
    // Check if record button is pressed from keypad!
    ///////////////////////////////////////////////////
    if (monster.keypadButtonPress(MONSTERSHIELD_KEYPAD_RECORD) == true)
    {
      // When calling recordAnimation(), the user will be prompted to make 3 choices:
      // 1.  First, the MonsterShield will begin flashing "b" and "-".  This is the bank selection menu.
      //      Choose 0, 1, 2, or 3 from the keypad (the out 1, out 2, out 3, and out 4 buttons on the keypad) and 
      //      then press the record button again.
      //
      // 2.  Next, the MonsterShield will begin flashing "r" and "-".  This is the relay selection menu.
      //      Press out 1, out 2, out 3, or out 4 followed by the record button to only record that track on that bank.
      //      You can also choose to program all 4 tracks on the selected bank at the same time by just pressing the
      //      record button without pressing any of the other buttons on the keypad.
      // 
      // 3.  Finally, the MonsterShield will begin flashing "c" and "-".  This is the record mode menu.
      //      Pressing out 1 and record will overlay recording on what was already previously recorded.
      //      Pressing out 2 and record will wipe the selected track(s) while keeping everything else.
      //      Pressing out 3 and record will wipe the entire animation slot and start from scratch.
      monster.recordAnimation(monster.getActiveSlot());
    }
    
  }
  
  
}

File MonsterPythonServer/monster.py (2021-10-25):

# Python 3 web server for MonsterShield
from http.server import BaseHTTPRequestHandler, HTTPServer
import time
import ssl
import os
#from gpiozero import LED
import serial

hostName = ""
"""hostName = "localhost" """
"""serverPort = 8080"""
serverPort = 4443
# note:  If you want to use TLS (HTTPS), then you will need to have a SSL
# cert (take a look at openssl to generate your own), and uncomment the
# socket lines at the end of the code and specify your cert files.

ser = None


enginespeed = 0.5
curspeed = 0.0

def connectToMonster():
    try:
        ser = serial.Serial('/dev/ttyACM0',115200)
    except:
        print("Can't Connect!")


def ReadData():
    if not ser is None:
        bytesToRead = ser.inWaiting()
        print(ser.read(bytesToRead))


time.sleep(5)
ReadData()

class MyServer(BaseHTTPRequestHandler):

    def do_GET(self):

        if ser is None:
            connectToMonster()

        if self.path == "/":

            root = os.path.join(os.path.dirname(os.path.dirname(os.path.abspath(__file__))), 'html')
            filename = 'indexmonster.html'
            self.send_response(200)
            self.send_header('Content-type', 'text/html')
            self.end_headers()

            with open(filename, 'rb') as fh:
                html = fh.read()
                #html = bytes(html, 'utf8')
                self.wfile.write(html)

        if self.path == "/s0":
            self.send_response(200)
            self.send_header("Content-type", "text/plain")
            self.end_headers()            
            self.wfile.write(bytes("Trigger #0", "utf-8"))
            if not ser is None:
                ser.write(b'@T0')

        if self.path == "/s1":
            self.send_response(200)
            self.send_header("Content-type", "text/plain")
            self.end_headers()            
            self.wfile.write(bytes("Trigger #1", "utf-8"))
            if not ser is None:
                ser.write(b'@T1')

        if self.path == "/s2":
            self.send_response(200)
            self.send_header("Content-type", "text/plain")
            self.end_headers()            
            self.wfile.write(bytes("Trigger #2", "utf-8"))
            if not ser is None:
                ser.write(b'@T2')

        if self.path == "/s3":
            self.send_response(200)
            self.send_header("Content-type", "text/plain")
            self.end_headers()            
            self.wfile.write(bytes("Trigger #3", "utf-8"))
            if not ser is None:
                ser.write(b'@T3')  

        if self.path == "/s4":
            self.send_response(200)
            self.send_header("Content-type", "text/plain")
            self.end_headers()            
            self.wfile.write(bytes("Trigger #4", "utf-8"))
            if not ser is None:
                ser.write(b'@T4') 

        if self.path == "/s5":
            self.send_response(200)
            self.send_header("Content-type", "text/plain")
            self.end_headers()            
            self.wfile.write(bytes("Trigger #5", "utf-8"))
            if not ser is None:
                ser.write(b'@T5')

        if self.path == "/s6":
            self.send_response(200)
            self.send_header("Content-type", "text/plain")
            self.end_headers()            
            self.wfile.write(bytes("Trigger #6", "utf-8"))
            if not ser is None:
                ser.write(b'@T6')  


        if self.path == "/s7":
            self.send_response(200)
            self.send_header("Content-type", "text/plain")
            self.end_headers()            
            self.wfile.write(bytes("Trigger #7", "utf-8"))
            if not ser is None:
                ser.write(b'@7')  


        if self.path == "/s8":
            self.send_response(200)
            self.send_header("Content-type", "text/plain")
            self.end_headers()            
            self.wfile.write(bytes("Trigger #8", "utf-8"))
            if not ser is None:
                ser.write(b'@T8')


        if self.path == "/s9":
            self.send_response(200)
            self.send_header("Content-type", "text/plain")
            self.end_headers()            
            self.wfile.write(bytes("Trigger #9", "utf-8"))
            if not ser is None:
                ser.write(b'@T9')


        if self.path == "/sa":
            self.send_response(200)
            self.send_header("Content-type", "text/plain")
            self.end_headers()            
            self.wfile.write(bytes("Trigger #A", "utf-8"))
            if not ser is None:
                ser.write(b'@Ta')


        if self.path == "/sb":
            self.send_response(200)
            self.send_header("Content-type", "text/plain")
            self.end_headers()            
            self.wfile.write(bytes("Trigger #B", "utf-8"))
            if not ser is None:
                ser.write(b'@Tb')


        if self.path == "/sc":
            self.send_response(200)
            self.send_header("Content-type", "text/plain")
            self.end_headers()            
            self.wfile.write(bytes("Trigger #C", "utf-8"))
            if not ser is None:
                ser.write(b'@Tc')

                      
        if self.path == "/sd":
            self.send_response(200)
            self.send_header("Content-type", "text/plain")
            self.end_headers()            
            self.wfile.write(bytes("Trigger #D", "utf-8"))
            if not ser is None:
                ser.write(b'@Td')


        if self.path == "/se":
            self.send_response(200)
            self.send_header("Content-type", "text/plain")
            self.end_headers()            
            self.wfile.write(bytes("Trigger #E", "utf-8"))
            if not ser is None:
                ser.write(b'@Te')


        if self.path == "/sf":
            self.send_response(200)
            self.send_header("Content-type", "text/plain")
            self.end_headers()            
            self.wfile.write(bytes("Trigger #F", "utf-8"))
            if not ser is None:
                ser.write(b'@Tf')
           

        if self.path == "/triggerson":
            self.send_response(200)
            self.send_header("Content-type", "text/plain")
            self.end_headers()            
            self.wfile.write(bytes("Triggers ON", "utf-8"))
            if not ser is None:
                ser.write(b'@i')

        if self.path == "/triggersoff":
            self.send_response(200)
            self.send_header("Content-type", "text/plain")
            self.end_headers()            
            self.wfile.write(bytes("Triggers OFF", "utf-8"))
            if not ser is None:
                ser.write(b'@I')
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

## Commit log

2016-01-05 Added the original Fritzing PCB CAD files and the exported Gerber layers so that folks can try their hand at building their own MonsterShield boards or modifying the design. At some point I hope to d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
    [MonsterShield_PROD_0.1B_001.fzz, keypad_V2.fzz]
2016-01-05 Added documentation source files and BOM (bill of materials)
    [MonsterShield BOM.ods]
2016-01-05 Added expansion board design. Don't recommend you build one of these without talking to me. I had to field modify them to fix a design flaw, and I'm not sure I ever redressed the issue in the design 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
    [Memory Mapping Chart.xlsx, MonsterExpanderR1-0-V018.fzz, MonsterExpanderR1-1-V000.fzz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]
2016-01-05 Added 1.5.0 Arduino Firmware
2021-10-25 Add support for disabling triggers
    Added the ability to disable (as in, ignore) triggers that are connected to the MonsterShield, and to later re-enable them. This can only be done via the serial port. Command to ignore all triggers (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
2021-10-25 Python Web Server for MonsterShield
    Simple Python web server interface that provides a web page that allows you to manually trigger any of the 15 sequences with a click of a button. You can run this on a Raspberry Pi and have the MonsterShield / Arduino connected to one of the Raspberry Pi USB ports. You will need to update the serial port to match the one you are using. i.e., replace the '' string below:
    ser = serial.Serial('/dev/ttyACM0',115200)
    Windows example:
    ser = serial.Serial('COM3',115200)
    If you intend to use an SSL cert, you will also need to uncomment the 4 lines near the end of the code and provide your cert files.
    [monster.py]
